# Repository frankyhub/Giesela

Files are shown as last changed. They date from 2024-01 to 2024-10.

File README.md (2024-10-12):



<div align="center">

|[:skull:ISSUE](https://github.com/frankyhub/Giesela/issues?q=is%3Aissue)|[:speech_balloon: Forum /Discussion](https://github.com/frankyhub/Giesela/discussions)|[:grey_question:WiKi](https://github.com/frankyhub/Giesela/wiki)||
|--|--|--|--|
| | | | |
||<a href="https://github.com/frankyhub/Giesela/issues">|<a href="https://github.com/frankyhub/Giesela/discussions">|<a href="https://github.com/frankyhub/Giesela/releases">|
|| <a href="https://github.com/frankyhub/Giesela/pulse" alt="Activity">| <a href="https://github.com/frankyhub/Giesela/graphs/traffic">  |<a href="https://github.com/frankyhub?tab=stars"> |
</div>

# Giesela Pflanzenbewässerung

Automatisches Bewässerungssystem

## Story

Hey, ich bin Giesela, ein automatisches Bewässerungssystem für drei unterschiedliche Pflanzentypen. Drei Sensoren erfassen die Feuchte der Pflanzenerde in den Blumentöpfen und steuern die Wasserzufuhr für die Pflanzenbewässerung. Sollte im Wassertank zu wenig Wasser sein, erkennt das der "Trockenschutzsensor" und die Füllstands-LED leuchtet. Gleichzeitig schalten die drei Pumpen aus, bis ausreichend Gießwasser nachgefüllt wurde.
Entsteht aus irgendeinem Grund zu viel Nässe in den Blumentöpfen, schalten zur Sicherheit die drei Pumpen ebenfalls ab, die Überlauf-LED leuchtet und der Buzzer ertönt.
An einem WEB-Server werden die drei Feuchtewerte der Pflanzentöpfe mit Analoganzeigen dargestellt.
Für die Inbetriebnahme steht ein WLAN-Manager zur Eingabe der WLAN-Zugangsdaten zur Verfügung. Nach dem ersten anlegen der Versorgungsspannung wird bei den WLAN-Netzwerkeinstellungen des Handys oder Tablets das Netzwerk "Giesela" ausgewählt und in der Adressleiste des Browsers die IP-Adresse 192.168.4.1 eingegeben. Mit dieser IP-Adresse startet er WLAN-Manager für die Eingabe und dem Speichern der WLAN-Zugangsdaten. Nach der Eingabe und dem Speichern der SSID und des WLAN-Passwortes startet der Micro Controller neu und baut die WLAN-Verbindung auf. Jetzt ist das Bewässerungssystem und der WEB-Server aktiv.

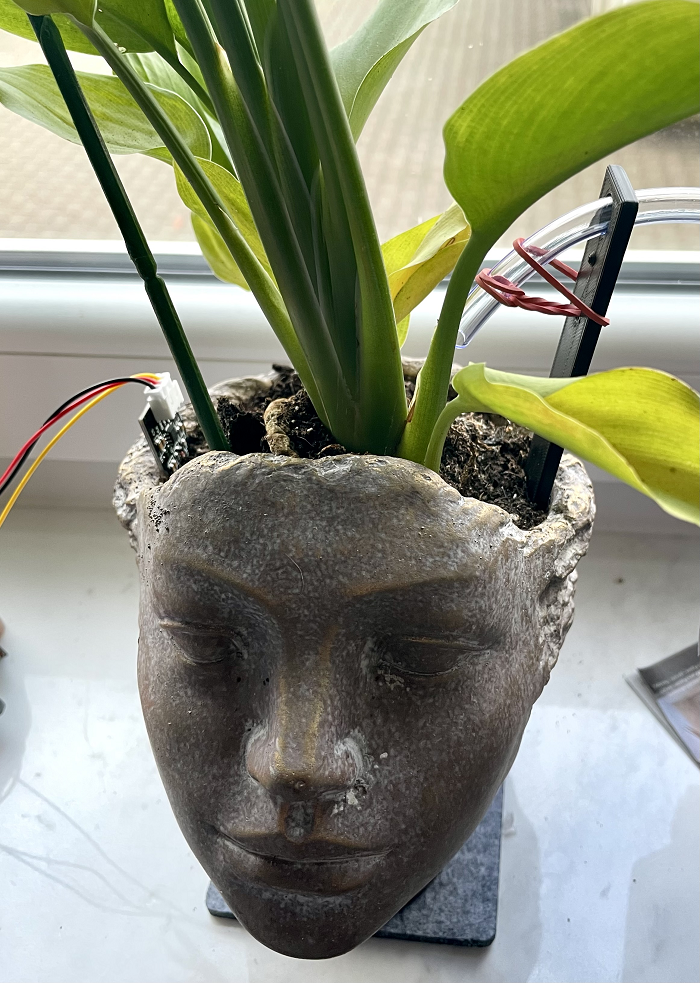
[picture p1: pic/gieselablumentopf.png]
Blumentopf


Giesela Pflanzenbewässerung

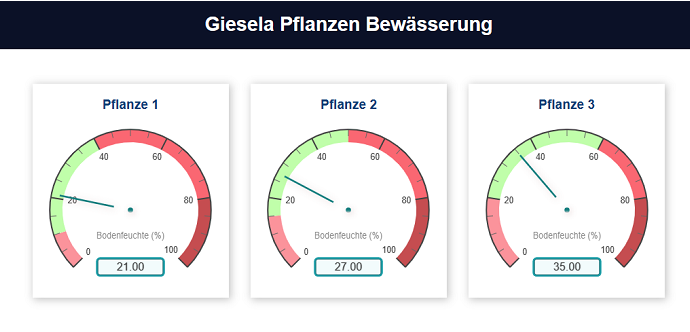
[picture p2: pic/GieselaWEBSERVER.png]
Giesela WEB-Server


Giesela WEB-Server

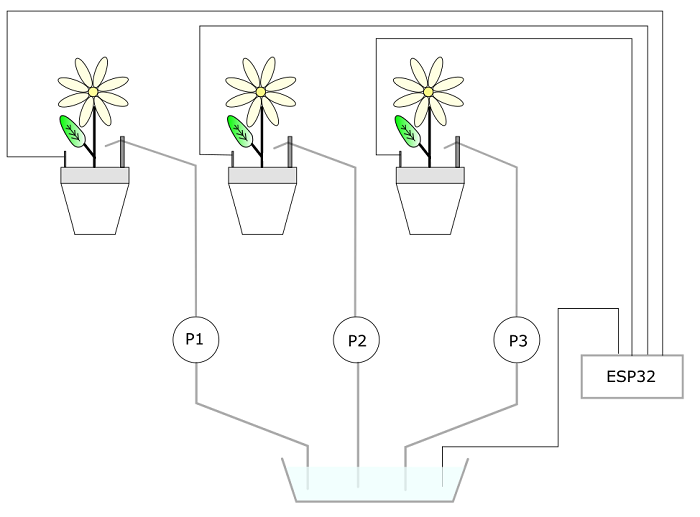
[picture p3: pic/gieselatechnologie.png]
Giesela Technologie-Schema


Giesela Technologie-Schema

---

## Hardware
Die Stückliste für Giesela:

+ 1 x ESP32
+ 1 x ESP32-Shield
+ 2 x Buchsenleisten
+ 2 x Stiftleisten
+ 1 x Schalter
+ 1 x Buzzer
+ 5 x 1,2 kOhm
+ 5 x LED rot
+ 5 x Relais
+ 3 x Pumpen
+ 3 x Bodensensoren
+ 1 x Füllstandssensor
+ 1 x Litze
+ 1 x 9V Netzteil
+ 1 x Gelasertes Gehäuse(4mm Sperrholz 600x300)

---

## Aufbau und Montage
Der Aufbau und die Montage des Bewässerungs-Systems ist in mehrere Schritte unterteilt.

Schritt 1: Das Gehäuse
+ Erstelle auf Boxes.PY eine "BasedBox" mit den Abmessungen x=110, y=100 und h=100.
+ Füge in die erstellte SVG-Grafik die Löcher für die LEDs und den Schalter ein
+ Füge in die erstellte SVG-Grafik die Ausgänge für die Sensoren und Pumpen ein
+ Füge in die erstellte SVG-Grafik den Ausschnitt für die ESP32 Spannungsversorgung ein
+ Schneide das Gehäuse mit dem Lasercutter aus
+ Montiere die Gehäuseteile zusammen (noch nicht verkleben)

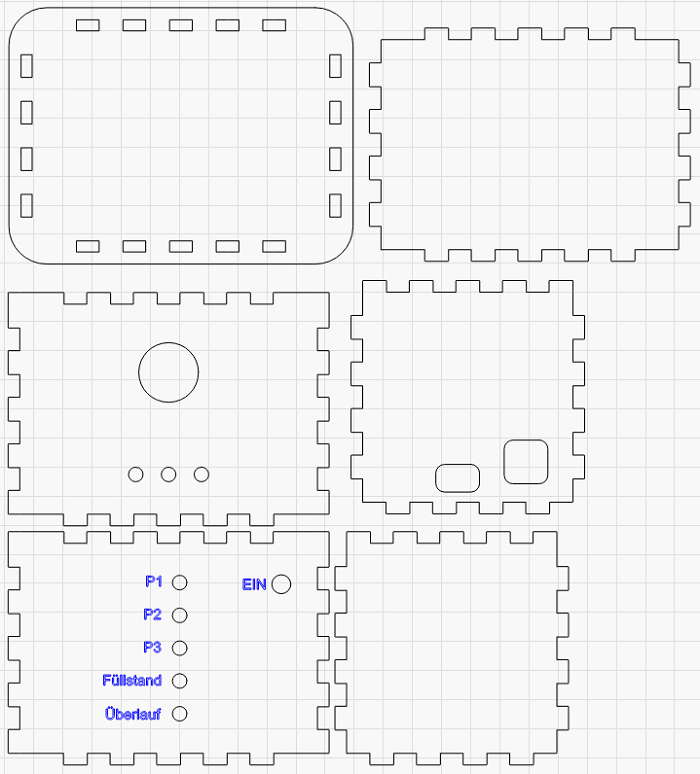
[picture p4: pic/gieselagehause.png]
Gieselagehause


Giesela Gehäuse.png

---

Schritt 2: 3D-Druck mit Tinkercad
+ Zeichne und drucke 4 Platinen Füße für den ESP32, D=5mm x 5mm
+ Klebe die Füße auf die Unterseite des ESP32-Shields
+ Zeichne und drucke 3 Schlauchhalter

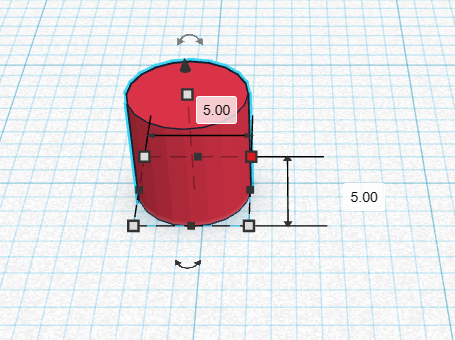
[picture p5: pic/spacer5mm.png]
Spacer5mm


5mm Spacer

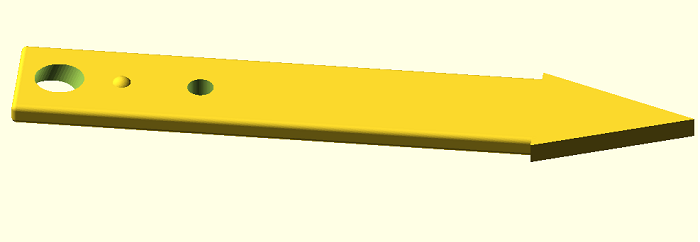
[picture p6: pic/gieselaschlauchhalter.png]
Gieselaschlachhalter


Schlauchhalter

---

Schritt 3: Verdrahtung und Lötarbeiten
+ Bestücke das ESP32-Shield mit den Buchsenleisten und den Vorwiderständen für die LEDs
+ Biege an einem Ende der Widerstände und am +Pol der LEDs eine Öse

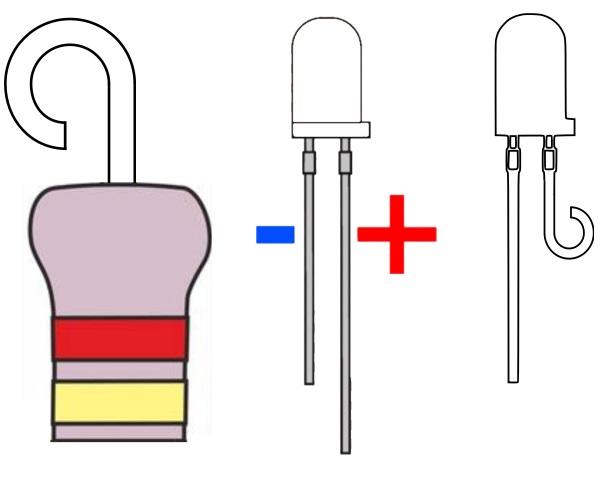
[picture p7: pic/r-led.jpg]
LED


LED Öse

Führe Anschlussdrähte für die Widerstände und der LEDs durch die Öse und Löte sie an

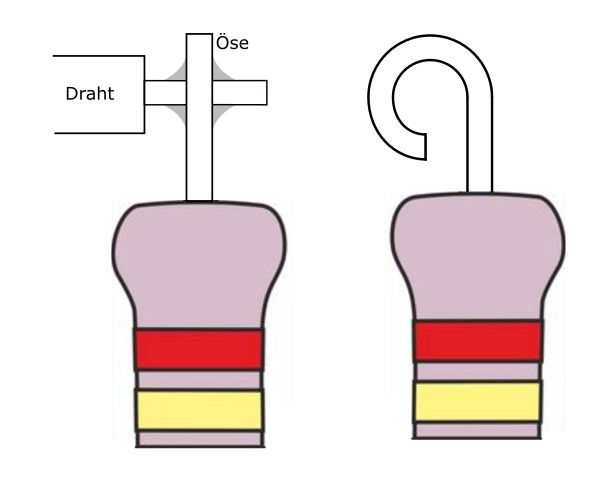
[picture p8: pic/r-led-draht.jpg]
LED-Draht


LED Lötstelle

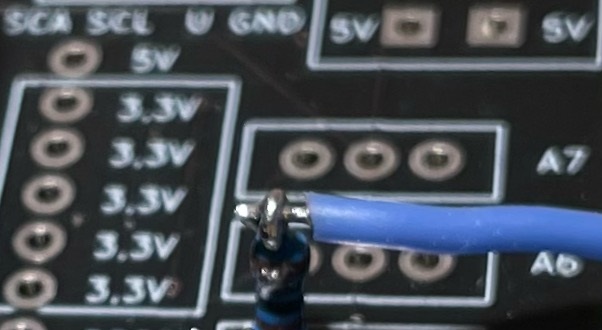
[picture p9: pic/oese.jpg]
Oese


Platine

Verdrahte das Shield, die LEDs, die Sensoren, die Pumpen, den Buzzer und die Relais nach den Verdrahtungsplan

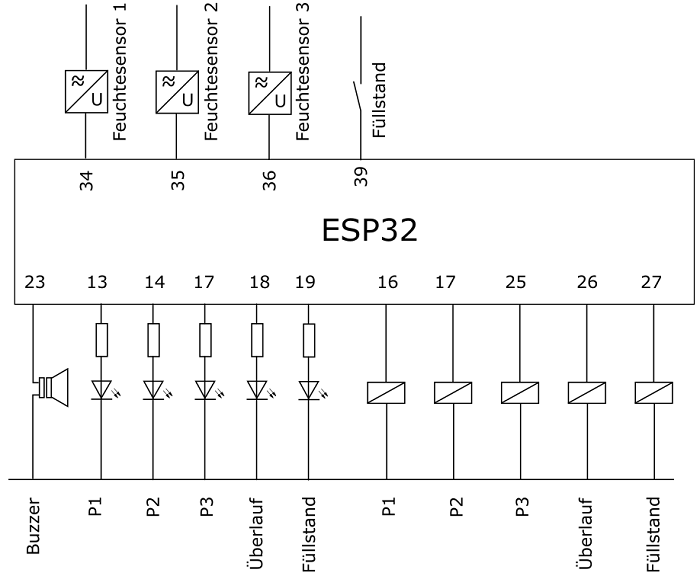
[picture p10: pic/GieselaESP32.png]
ESP32


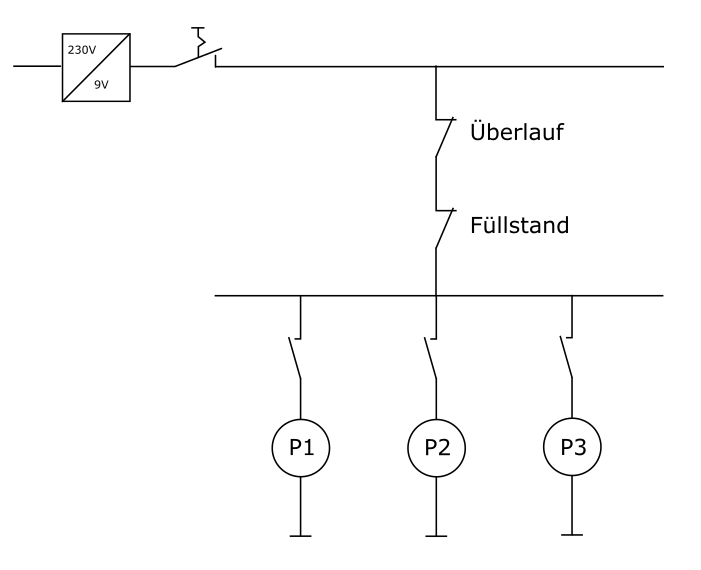
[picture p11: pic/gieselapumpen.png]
Ggieselapumpen


---

Schritt 4: Inbetriebnahme
+ Kontrolliere alle Verbindungen
+ Lade das Programm in den ESP32
+ Das Programm befindet sich auf deinen Laptop unter Nextcloud/Giesela
+ Versorge Giesela mit Spannung
+ Gib über den WLAN-Manager die WLAN-Zugangsdaten ein
+ Teste den WEB-Server
+ Simuliere die Feuchtesensoren mit einem Poti
+ Wenn der WEB-Server funktioniert, schließe die Feuchtesensoren an
+ Montiere alle Bauteile in das Gehäuse
+ Teste die Funktion der Pumpen und der Alarmmeldungen
+ Beobachte die Gießfunktion und achte darauf, dass kein Wasser unkontrolliert austritt

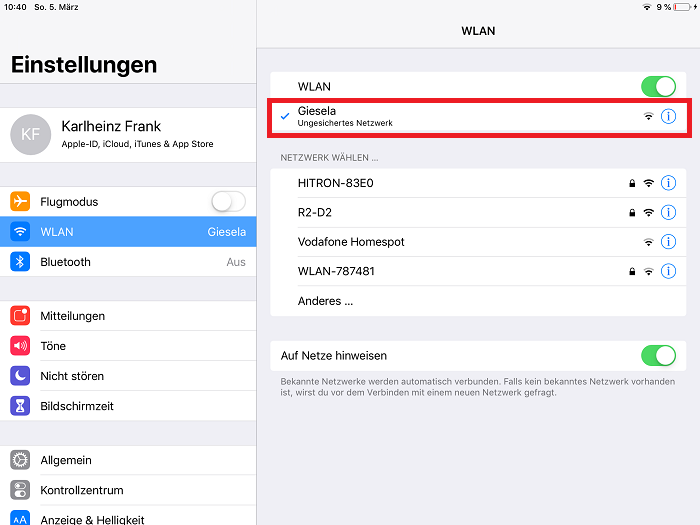
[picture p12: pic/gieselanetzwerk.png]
Gieselanetzwerk


Giesela im WLAN-Netzwerk auswählen

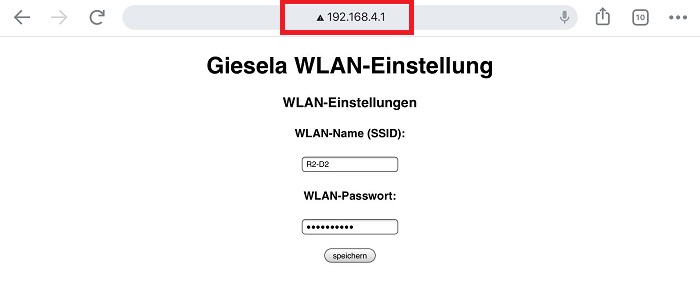
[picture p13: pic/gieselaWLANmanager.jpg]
Gieselawlanmanager


Die WLAN-Zugangsdaten im WLAN-Manager eingeben und speichern.

---

<div style="position:absolute; left:2cm; ">   
<ol class="breadcrumb" style="border-top: 2px solid black;border-bottom:2px solid black; height: 45px; width: 900px;"> <p align="center"><a href="#oben">nach oben</a></p></ol>
</div>  

---

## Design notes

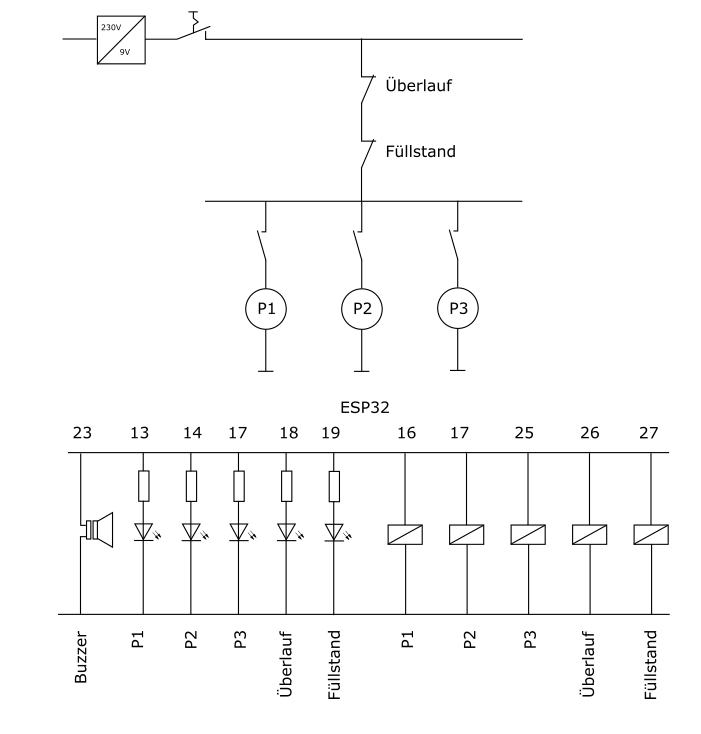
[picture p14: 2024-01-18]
pic/gieselaschaltplan.png

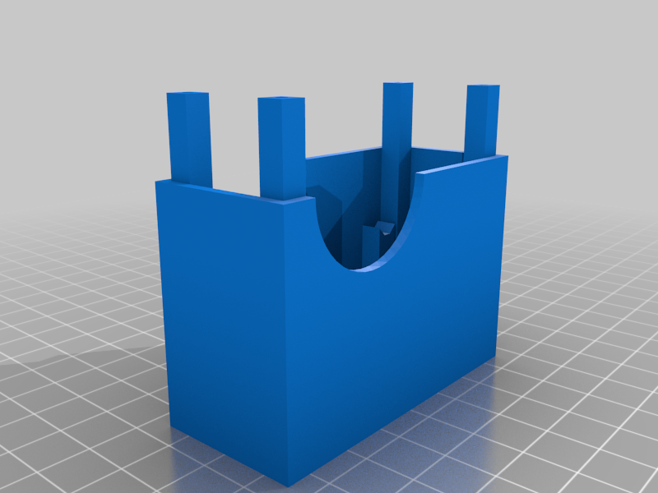
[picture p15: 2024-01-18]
3D/images/Ventil2.png

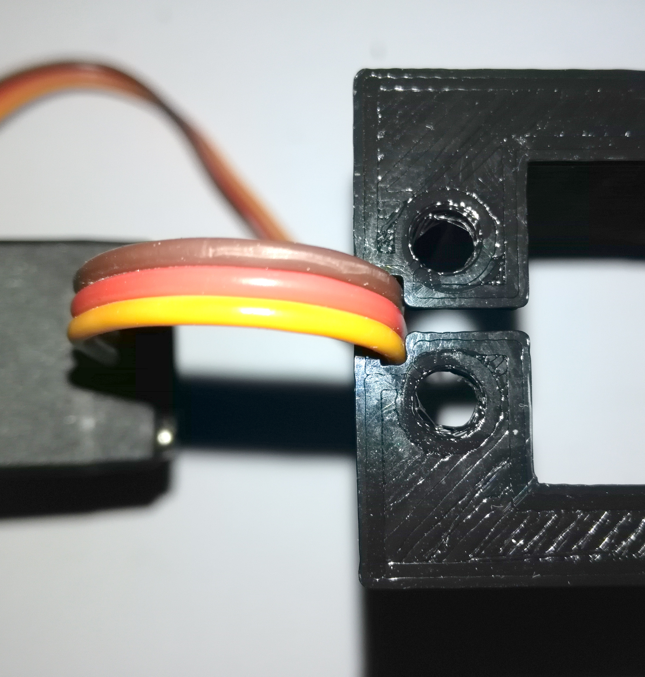
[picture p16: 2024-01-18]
3D/images/Abbildung91.jpg

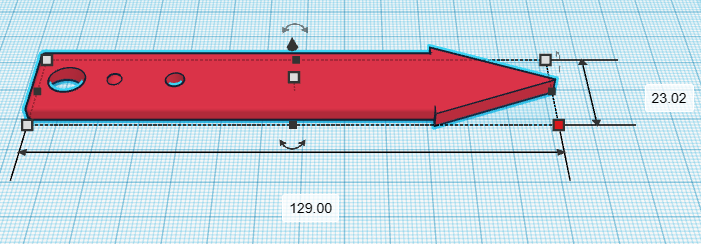
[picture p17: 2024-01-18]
pic/gieselaschlachhalt.png

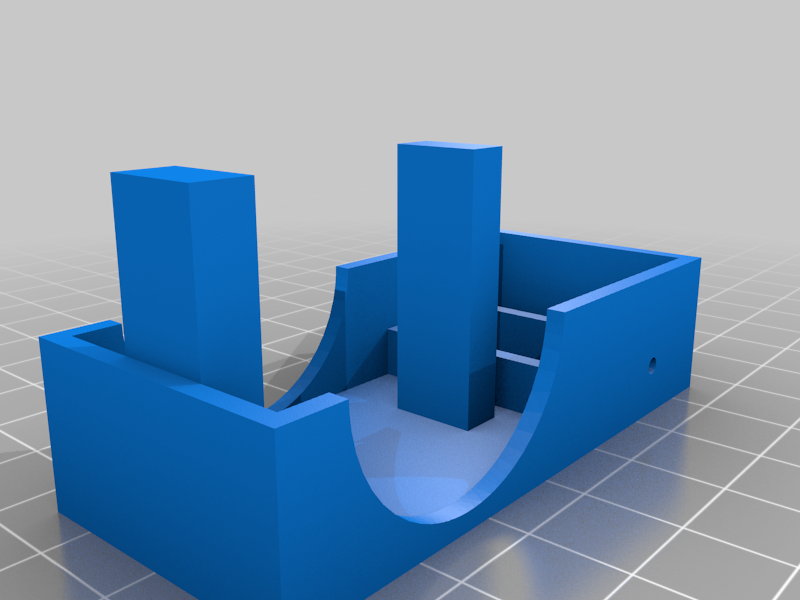
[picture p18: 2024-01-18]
3D/images/Ventil1.png

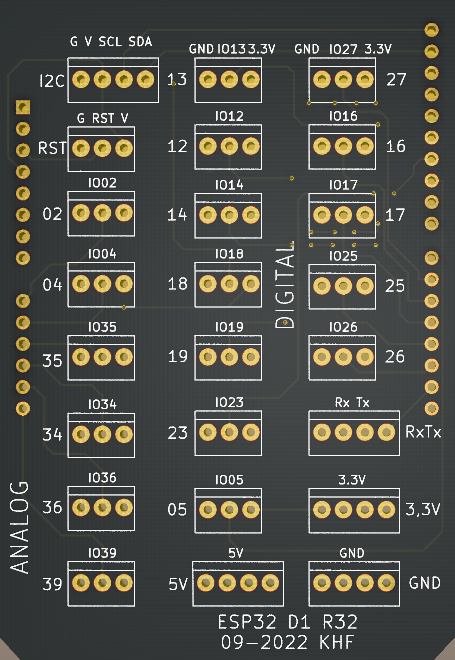
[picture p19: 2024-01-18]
pic/ESP32Shield09-22.png

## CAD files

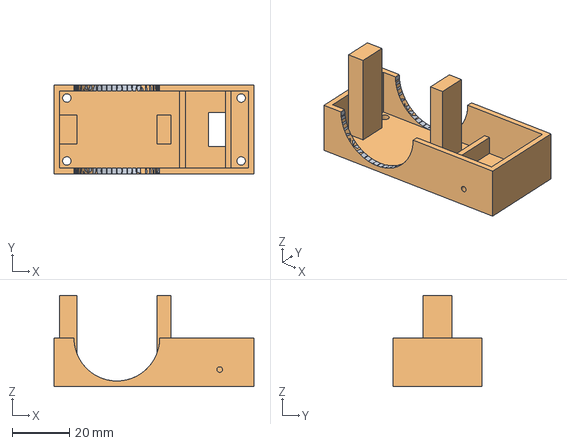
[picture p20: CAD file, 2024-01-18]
3D/files/Ventil1.FCStd
70.0 x 31.0 x 32.0 mm
Fusion001 (Meshed)

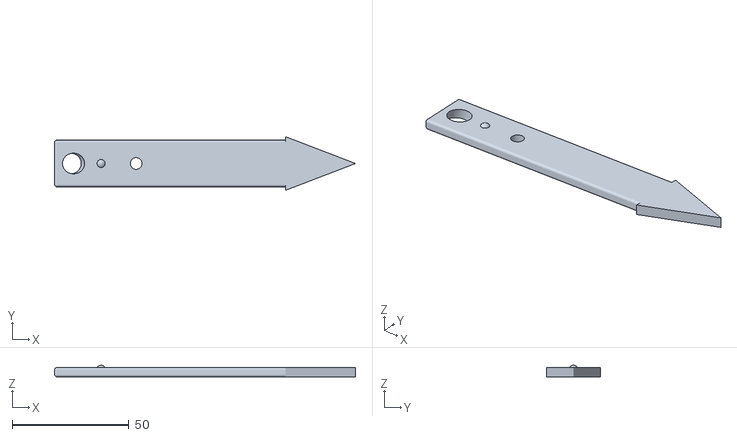
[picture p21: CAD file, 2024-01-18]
3D/Schlauchhalter/Schlauchhalter.stl
129.0 x 23.0 x 5.00

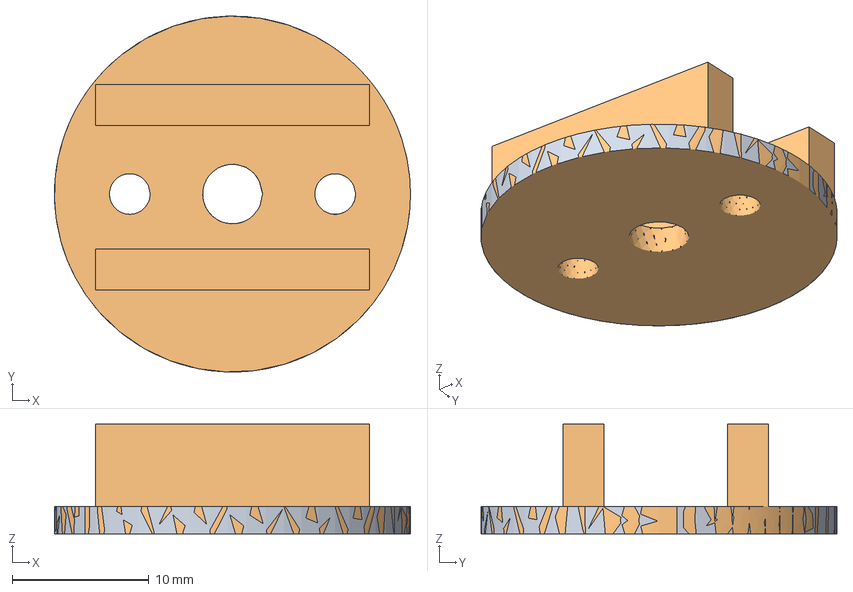
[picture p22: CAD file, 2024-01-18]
3D/files/servo_adapter_v.FCStd
26.0 x 26.0 x 8.00 mm
Fusion (Meshed)

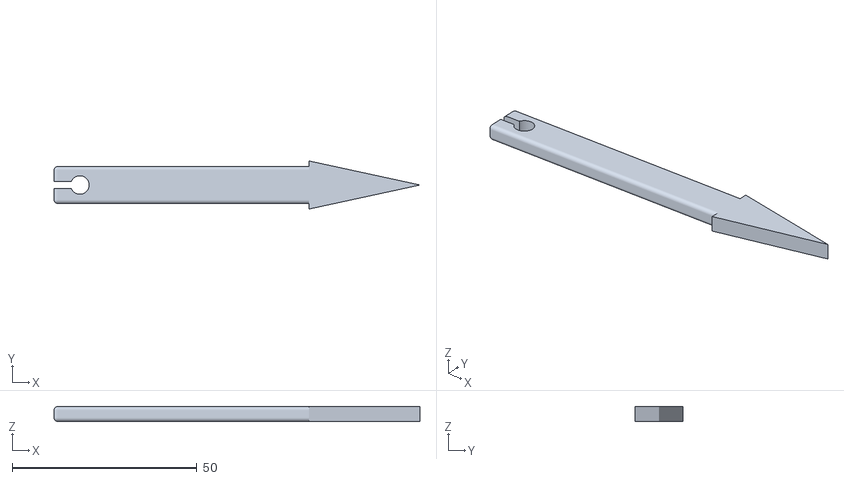
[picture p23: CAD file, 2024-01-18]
3D/Schlauchhalter/Sensorhalter.stl
99.0 x 13.0 x 4.00

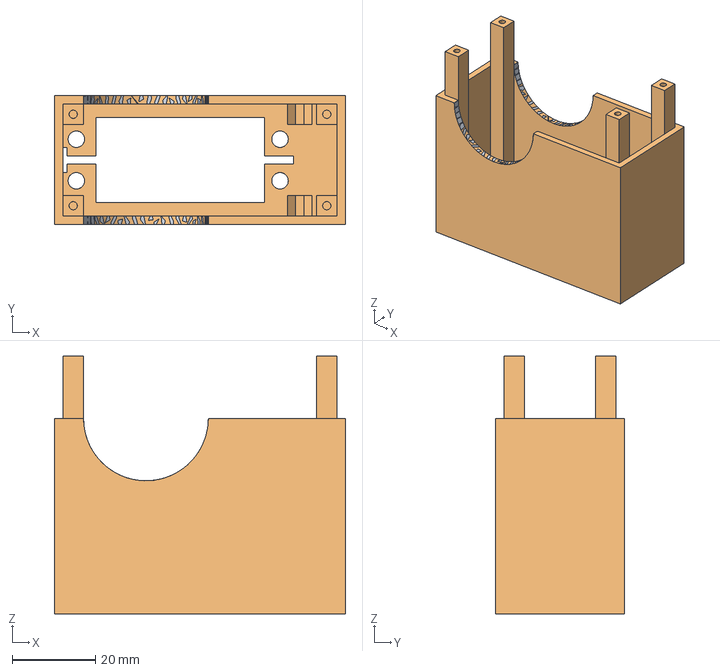
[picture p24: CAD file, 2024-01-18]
3D/files/Ventil2.FCStd
70.0 x 31.0 x 62.0 mm
Fusion (Meshed)

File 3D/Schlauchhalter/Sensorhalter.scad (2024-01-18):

/*
*******************************************
Objekt Info: Sensorhalter
                Ecken abrunden mit cuboid
                polygon

*******************************************
Version: 14.03.2023 khf
//***************   Auswahl   *************
keine
//*****************************************

//***************   Libraries  ************/
include <lib/std.scad>
//*****************************************/

//***************  Parameter   *************
//keine
//**************   Programm  **************/

//Dreieck
translate(v = [34, 0, -2]) { 
    linear_extrude(height = 4)
polygon(
 points=[
 [0,0],    // Punkt 0
 [0,6.5],  // Punkt 1
 [30,0], // Punkt 2
 [0,-6.5]   // Punkt 3
    
],
 paths=[
 [0,1,2,3] // 4 Verbindungen
]
);
}



//Grundkoerper
difference() {
cuboid(
    [70,10,4], rounding=1,
    edges=[
    TOP+FRONT,
    TOP+BACK,
    TOP+LEFT,
//    TOP+RIGHT,
    
    DOWN+FRONT,
    DOWN+BACK,
    DOWN+LEFT,
//    DOWN+RIGHT,
    
    FRONT+RIGHT,
    FRONT+LEFT,
    
    BACK+LEFT,
    BACK+RIGHT,
        
    ],
    $fn=60
);    

//Loch oben    
translate(v = [-28, 0, -5]) { 
cylinder(h = 10, r1 = 2.5, r2 = 2.5,$fn=50);
}  
//Kabelschlitz
 translate(v = [-36, -1, -5]) { 
cube(size = [6,2,10]);
 }
}

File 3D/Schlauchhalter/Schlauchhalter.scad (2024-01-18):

/*
*******************************************
Objekt Info: Schlauchhalter
                Ecken abrunden mit cuboid
                polygon

*******************************************
Version: 14.03.2023 khf
//***************   Auswahl   *************
keine
//*****************************************
//***************   Libraries  ************/
include <lib/std.scad>
//*****************************************/

//***************  Parameter   *************
//keine
//**************   Programm  **************/

//Polygon
translate(v = [49, 0, -2]) { 
    linear_extrude(height = 4)
polygon(
 points=[
 [0,0],     // Punkt 0
 [0,11.5],  // Punkt 1
 [30,0],    // Punkt 2
 [0,-11.5]  // Punkt 3
    
],
 paths=[
 [0,1,2,3] // 4 Verbindungen
]
);
}

//Grundkoerper
difference() {
cuboid(
    [100,20,4], rounding=1,
    edges=[
    TOP+FRONT,
    TOP+BACK,
    TOP+LEFT,
//    TOP+RIGHT,
    
    DOWN+FRONT,
    DOWN+BACK,
    DOWN+LEFT,
//    DOWN+RIGHT,
    
    FRONT+RIGHT,
    FRONT+LEFT,
    
    BACK+LEFT,
    BACK+RIGHT,
        
    ],
    $fn=60
);    

//Schlauchloch oben    
rotate([0, 20, 0]) { 
translate(v = [-40, 0, -25]) { 
cylinder(h = 20, r1 = 4.5, r2 = 4.4,$fn=50);
} 
} 
//Loch fuer Gummiband
translate(v = [-15, 0, -15]) { 
cylinder(h = 20, r1 = 2.5, r2 = 2.5,$fn=50);
    }
}
//Markierung in Richtung Pflanze
translate(v = [-30, 0, 1]) { 
sphere(r = 2,$fn=50);
}
    

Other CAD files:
3D/files/Ventil1.stl
3D/files/Ventil2.stl
3D/files/servo_adapter_v.stl

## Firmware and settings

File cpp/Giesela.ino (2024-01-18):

/*************************************************************************************************
                                      PROGRAMMINFO
**************************************************************************************************
  Funktion: Giesela; ESP32 WEB Server fuer eine Bewaessungsanlage mit WLAN-Manager
**************************************************************************************************
  Version: 13.03.2023
**************************************************************************************************
  Board: ESP32vn IoT UNO V1.0.4
**************************************************************************************************
  C++ Arduino IDE V1.8.13
**************************************************************************************************
  Einstellungen:
  https://dl.espressif.com/dl/package_esp32_index.json
  http://dan.drown.org/stm32duino/package_STM32duino_index.json
  https://raw.githubusercontent.com/espressif/arduino-esp32/gh-pages/package_esp32_dev_index.json
**************************************************************************************************
  Librarys
  - WiFi.h V0.16.1
**************************************************************************************************/


#include <Arduino.h>
#include <WiFi.h>
#include <AsyncTCP.h>
#include <ESPAsyncWebServer.h>
#include "SPIFFS.h"
#include <Arduino_JSON.h>


/*
// Set LED GPIO
const int ledPin = 2;
// Stores LED state
String ledState;
*/


AsyncWebServer server(80);
AsyncEventSource events("/events");

JSONVar readings;

unsigned long lastTime = 0;
unsigned long timerDelay = 10000;


int humidity10 = 0;
int humidity20 = 0;
int humidity30 = 0;

int pumpe1 = 16;
int pumpe2 = 17;
int pumpe3 = 25;

//Überschwemmung!
int buzzer = 13;

//Wasserstand im Vorratstank
int sensorLED = 19;
int wassersensor = 39;
int wasserstand;
int ueberschwemmung;


String getSensorReadings() {

  readings["STATE"] = String(digitalRead(buzzer));
//  readings["humidity1"] = String(map(analogRead(34), 4096, 0, 0, 100)-40); //Feuchtesensor
  readings["humidity1"] = String(map(analogRead(34), 4096, 0, 100, 0));  //Poti
  readings["humidity2"] = String(map(analogRead(35), 4096, 0, 100, 0));
  readings["humidity3"] = String(map(analogRead(36), 4096, 0, 100, 0));


  int humiditya = map(analogRead(34), 4096, 0, 100, 0); //Poti
  Serial.print("Bodenfeuchte 1: ");
  Serial.println(humiditya);


  int humidityb = map(analogRead(35), 4096, 0, 100, 0);
  Serial.print("Bodenfeuchte 2: ");
  Serial.println(humidityb);


  int humidityc = map(analogRead(36), 4096, 0, 100, 0);
  Serial.print("Bodenfeuchte 3: ");
  Serial.println(humidityc);


  if (humiditya < 10) {
    digitalWrite(pumpe1, HIGH);
    Serial.println("Pumpe 1 AN");
  } else {
    digitalWrite(pumpe1, LOW);
    Serial.println("Pumpe 1 AUS");
  }

  if (humidityb < 15) {
    digitalWrite(pumpe2, HIGH);
    Serial.println("Pumpe 2 AN");
  } else {
    digitalWrite(pumpe2, LOW);
    Serial.println("Pumpe 2 AUS");
  }

  if (humidityc < 20) {
    digitalWrite(pumpe3, HIGH);
    Serial.println("Pumpe 3 AN");
  } else {
    digitalWrite(pumpe3, LOW);
    Serial.println("Pumpe 2 AUS");
  }

  if ((humiditya > 80)|| (humidityb > 80) || (humidityc > 80)) {
    digitalWrite(buzzer, HIGH);
    Serial.println("ALARM Bodenfeuchte > 80%");
  } else {
    digitalWrite(buzzer, LOW);
    Serial.println("ALARM AUS Bodenfeuchte < 80%");
  }


  wasserstand = digitalRead(wassersensor);
  
    if (wasserstand == HIGH) {
    digitalWrite(sensorLED, HIGH);
    Serial.println("Wasser nachfüllen!");
  } else {
    digitalWrite(sensorLED, LOW);
    Serial.println("Wasserstand OK");
  }

    ueberschwemmung = digitalRead(buzzer);
    if (ueberschwemmung == HIGH) {
   // digitalWrite(sensorLED, HIGH);
    Serial.println("Überschwemmung!");
  } else {
 //   digitalWrite(sensorLED, LOW);
    Serial.println("Keine Überschwemmung");
  }
  




  

  
  String jsonString = JSON.stringify(readings);
  return jsonString;

  

}





//SPIFFS
void initSPIFFS() {
  if (!SPIFFS.begin()) {
    Serial.println("Beim Mounten von SPIFFS ist ein Fehler aufgetreten");
  }
  Serial.println("SPIFFS erfolgreich geladen");
}

//WiFi
void initWiFi() {
        //init WiFi
  Serial.println("Connecting to WiFi");
  while (!makeWLAN()) {
    Serial.println("Cannot connect :(");
    delay(1000);
  }
}






void setup() {

  pinMode(pumpe1, OUTPUT);
  pinMode(pumpe2, OUTPUT);
  pinMode(pumpe3, OUTPUT);

  pinMode(buzzer, OUTPUT);

   pinMode(sensorLED, OUTPUT);
  pinMode(wassersensor, INPUT_PULLUP); 

  Serial.begin(115200);





  // Initialize SPIFFS
  if(!SPIFFS.begin(true)){
    Serial.println("An Error has occurred while mounting SPIFFS");
    return;
  }


  initWiFi();
  initSPIFFS();

  server.on("/", HTTP_GET, [](AsyncWebServerRequest * request) {
    request->send(SPIFFS, "/index.html", "text/html");

  });
;

  server.serveStatic("/", SPIFFS, "/");

  server.on("/readings", HTTP_GET, [](AsyncWebServerRequest * request) {
    String json = getSensorReadings();
    request->send(200, "application/json", json);
    json = String();
  });

  events.onConnect([](AsyncEventSourceClient * client) {
    if (client->lastId()) {
      Serial.printf("Client wieder verbunden! Die letzte Nachrichten-ID, die es erhalten hat, ist: %u\n", client->lastId());
    }
    //   client->send("Hallo!", NULL, millis(), 10000);
    client->send("Hallo!", NULL, millis(), 3000);
  });
  server.addHandler(&events);



  // Start server
  server.begin();
}

void loop() {

  if ((millis() - lastTime) > timerDelay) {
    // Sende Sensor Daten alle 10 Sek.
    events.send("ping", NULL, millis());
    events.send(getSensorReadings().c_str(), "new_readings" , millis());
    lastTime = millis();
  }
}

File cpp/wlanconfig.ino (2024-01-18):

/* ***********************************************************************
 *  Dies dient zur Konfiguration und zum Aufbau einer WLAN-Verbindung
 *  
 *  - Laden der Zugangsdaten aus dem Flash
 *       - ssid
 *       - password
 *       - ntpserver
 *  - Versuch eine Verbindung mit diesen Anmeldeinformationen herzustellen
 *  - Wenn eine Verbindung möglich ist, wird folgendes passieren:
 *      - eine Änderung im AP-Modus (NICHT neu gestartet!!!)
 *      - Aufruf des WLAN-Managers http://192.168.4.1
 *      - zeigt HTML-Code aus wlanconf.h mit ausgefüllten Anmeldeinformationen an
 *      - Benutzer speichert die Zugangsdaten
 *      - Beim Absenden des Formulars per Absenden werden die Anmeldeinformationen in Flash aktualisiert (ONLÝ THEN*)
 *      - Startet im Stationsmodus neu und beginnt den nächsten Versuch, sich mit den neuen Zugangdaten zu verbinden
 *  => Dies geschieht unendlich, bis eine Verbindung hergestellt werden kann.
 *      
 *  Es wird beim Aufruf von "makeWLAN()" (usaly in 'setup()') verwendet.
 *  Es wirdt "true" zurückgegeben, wenn die Verbindung erfolgreich war
 *  
 *  Libraries:
 *    - Wifi.h
 *    - Preferences.h
 *    - ESPAsyncWebServer.h
 *  
 *  Die WLAN-Instanz heißt "WiFi"
 *  Die Webserver-Instanz (nur im AP-Modus) heißt "Server"
 *  
 *  Wenn TESTMODUS wahr ist, wird nach einer erfolgreichen Verbindung ein falsches Passwort in Flash gespeichert. Also
 *  es stellt nach dem nächsten Neustart keine Verbindung her und startet den Vorgang von Anfang an.
 *  
 *  *: Wenn das WLAN offline ist und der ESP32 deshalb nach neuen Daten fragt, kannst du es ignorieren.
 *     Starte den ESP32 neu, wenn dein WLAN wieder verfügbar ist. Die Anmeldeinformationen ändern sich erst, wenn
 *     sie neu abgespeichert wurden.
 */

#include <WiFi.h>
#include <Preferences.h>
//#include "ESPAsyncWebServer.h"

#include "wlanconf.h"  //HTML-code fuer WLAN-setup

#define TESTMODUS false

// Webserver on port 80
//AsyncWebServer server(80);

// WLAN credentials
Preferences preferences;
String ssid;
String password;
String ntpserver;
int    bootAsAP;
#define MAXWLANTRY 10  // AP-Modus nach neuen Anmeldeinformationen fragen

// ### Im 'setup() aufrufen'
int makeWLAN()
{
  preferences.begin("credentials", false);

  ssid = preferences.getString("ssid", ""); 
  password = preferences.getString("password", "");
  ntpserver = preferences.getString("ntpserver", "de.pool.ntp.org");
    
  delay(250);
  Serial.println(F("Giesela: "));
  Serial.println(ssid);

  int tryCount = 0;
  if (ssid == "" || password == ""){
    Serial.println("Keine WLAN-Logindaten gespeichert!");
    ssid = "blub"; password = "blah";
    tryCount = MAXWLANTRY;
  }

  if (tryCount < MAXWLANTRY) {
    // Mit Wi-Fi verbinden
    WiFi.mode(WIFI_STA);
    WiFi.begin(ssid.c_str(), password.c_str());
    Serial.print("Verbinde mit WiFi ..");
    while ((WiFi.status() != WL_CONNECTED) && (tryCount<MAXWLANTRY)) {
      Serial.print('.');
      delay(1000);
      tryCount++;
    }
    IPAddress lip(0,0,0,0);
    if (WiFi.localIP() == lip) {
      tryCount = MAXWLANTRY;
    }
  }

  if (tryCount < MAXWLANTRY) {
    Serial.print(F("IP-Adresse per DHCP ist "));
    Serial.println(WiFi.localIP());  
    // Für den Automatik-Test
    if (TESTMODUS) {
      preferences.putString("password", "XXX"); 
    }
    return(true);   // Wenn die Verbindung in Ordnung ist, stoppe hier und kehre zurück
  }

  // Wenn keine Verbindung möglich ist, starte die Konfigurationswebsite im AP-Moduse 
  makeConfigAP();

  return(false);    
                   
}


// ### Baut eine eigene "WLAN-WEB-CAM" auf und startet unter http://192.168.4.1 ein Webinterface
// Diese Funktion läuft in der Schleife, bis neue Anmeldeinformationen gegeben sind - in diesem Fall startet sie neu
void makeConfigAP() {

  Serial.print("Erstelle AP (Access Point)…");
  WiFi.mode(WIFI_AP);
  delay(500);  
  WiFi.softAP("Giesela");

  IPAddress IP = WiFi.softAPIP();
  Serial.print("AP IP address: ");
  Serial.println(IP);
  
  server.on("/", HTTP_ANY, [](AsyncWebServerRequest *request){

    int paramsNr = request->params();
    Serial.println(paramsNr);
    String ssid = "";
    String password = "";
    int paramCountOk = 0;
    int gotAnswer = false;
  
    for(int i=0;i<paramsNr;i++){
  
      AsyncWebParameter* p = request->getParam(i);
      Serial.print("Param name: ");
      Serial.println(p->name());
      Serial.print("Param value: ");
      Serial.println(p->value());
      Serial.println("------");
      if (p->name() == "ssid") {
        ssid = p->value();
        paramCountOk++;
      }
      if (p->name() == "password") {
        password = p->value();
        paramCountOk++;
      }
      // is used for my clock-projects :) and
      // here commented out in HTML-code.
      if (p->name() == "ntpserver") {   
        ntpserver = p->value();
        paramCountOk++;
      }

      if (paramCountOk >= paramsNr) {
        preferences.putString("ssid", ssid); 
        preferences.putString("password", password); 
        preferences.putString("ntpserver", ntpserver); 
        preferences.putInt("bootAP", 0); 
        preferences.end();
        gotAnswer = true;
      }
    }
  
    String s = MAIN_page; //HTML-Inhalte lesen
    if (gotAnswer) {
      s.replace("*mark1begin*", "<!--");
      s.replace("*mark1end*", "-->");
      s.replace("*feedback*", "<div style='color:#CC0000'><h1>Verbindung wird versucht...</h1><h2>Sollte die Wetterstation nicht starten, bitte in 20 Sek. wieder mit dem WLAN Wetterstation verbinden und diese Seite neu aufrufen.</h2></div>");
    } else {
      s.replace("*mark1begin*", "");
      s.replace("*mark1end*", "");
      s.replace("*feedback*", "");
      s.replace("*ssid*", preferences.getString("ssid", ""));
      s.replace("*password*", preferences.getString("password", ""));
      s.replace("*ntpserver*", preferences.getString("ntpserver", ""));
    }
    request->send(200, "text/html", s);
    if (gotAnswer) {
      delay(3000);
      ESP.restart();
    }

  }); 
  server.begin();        // Server start
  Serial.println("HTTP-Server gestartet");

  serverLoop();
}

// ### Eine einfache Schleife zur Anzeige des Status auf dem seriellen Monitor, dass der WLAN-Manager läuft
void serverLoop() {
  while (true) {
    delay(1000);
    Serial.println("Der WiFi Manager ist aktiv ... 192.168.4.1");
  }
}
